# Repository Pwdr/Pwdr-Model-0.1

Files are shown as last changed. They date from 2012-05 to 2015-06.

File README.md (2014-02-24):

#Pwdr Model 0.1

Pwdr is an open source powder-based rapid prototyping machine. Its goal is to promote experiments and innovations in powder-based rapid-prototyping. The machine is ready to use both the 3DP as the SLS process with minimal adaption, although the printer is currently prepped for 3DP.

##Hardware

The Pwdr Model 0.1 consists of chassis, tool head and electronics. The printer entirely consists of off-the-shelf components. It has a simple design and can be built within a couple of hours. The machine is easy and affordable to build and modify. Building a Pwdr Model 0.1 machine costs about €1000,-.

##Software

The accompanying software for the Pwdr Model 0.1 converts the CAD model in a printable format. This file is then uploaded to the Pwdr Model 0.1 micro-controller. The machine is controlled by easy-to-use software that allow full control of the printing process.The Pwdr Model 0.1 software has been based on open source tools like [Arduino](http://arduino.cc) and [Processing](http://processing.org).

##Materials

A whole new range of materials become available for experimenting with open-source rapid-prototyping; for example, when using the 3DP process: gypsum, ceramics, concrete, sugar, etc. And when the SLS process is fully supported, plastic materials like ABS, PP, Nylon and metals become available as building material.A Hewlett Packard inkjet cartridge is used for the deposition of binder. The cartridge can be refilled with custom binders using a syringe. A custom binder of 20% alcohol and 80% water has been proven to work.

##Specifications

- Maximum build size: 125mm x 125mm x 125mm
- Print resolution (3DP): 96DPI
- Minimum vertical step size: 50μm
- Speed (depending on printed part): ±1 minute per layer

### License
This work is licensed under the Creative Commons Attribution-NonCommercial 3.0 Unported License. To view a copy of this license, visit http://creativecommons.org/licenses/by-nc/3.0/.

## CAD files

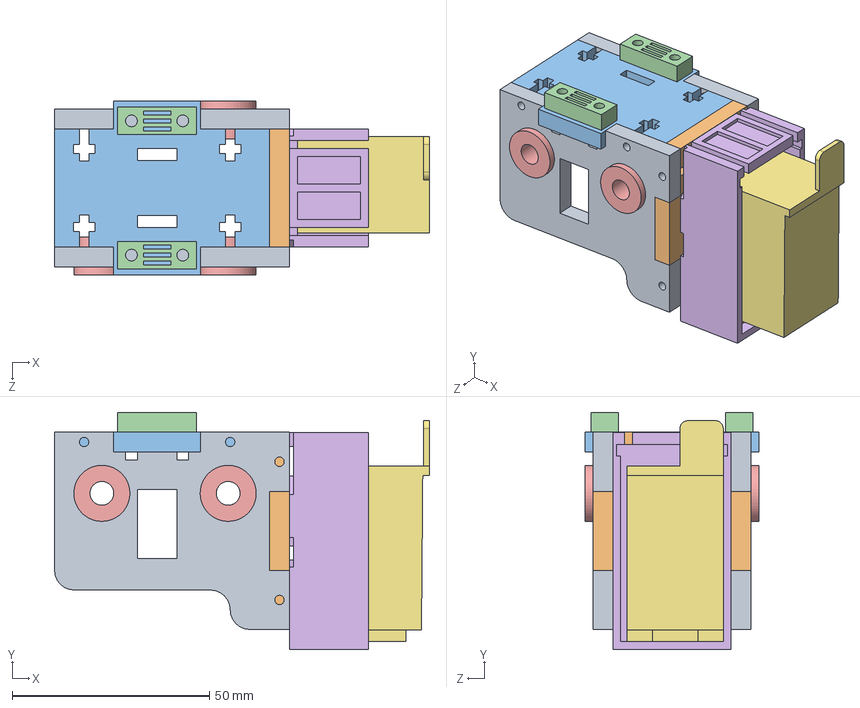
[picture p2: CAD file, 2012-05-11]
CAD drawings/Solidworks/Pwdr - Model 0.1 - XYcarriageMiddle.SLDASM
95.0 x 60.1 x 44.0 mm
Pwdr - Model 0.1 - XYcarriage4 x 2
Pwdr - Model 0.1 - XYcarriage5
Pwdr - Model 0.1 - XYcarriage6
Pwdr - Model 0.1 - XYcarriage7 x 2
Pwdr - Model 0.1 - BronzeBushing6mm x 3
HPC6402CartridgeHolder
HPC6402Cartridge
Pwdr - Model 0.1 - BrassInsert x 4

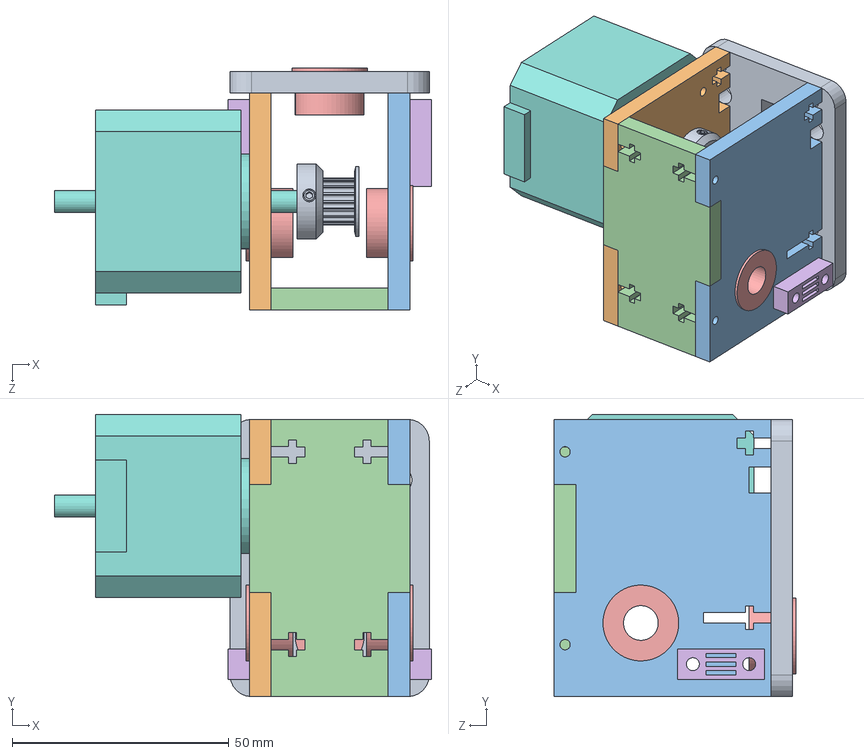
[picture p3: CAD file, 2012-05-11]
CAD drawings/Solidworks/Pwdr - Model 0.1 - XYcarriageLeft.SLDASM
87.0 x 65.2 x 55.8 mm
Pwdr - Model 0.1 - XYcarriage1
Pwdr - Model 0.1 - XYcarriage2Var
Pwdr - Model 0.1 - XYcarriage2Var2
Pwdr - Model 0.1 - XYcarriage3VAR
Pwdr - Model 0.1 - BronzeBushing10nn x 3
Pwdr - Model 0.1 - XYcarriage7 x 2
Pwdr - Model 0.1 - BrassInsert x 4
Nanotec - ST4209S1006-B
A6A51M018DF0606

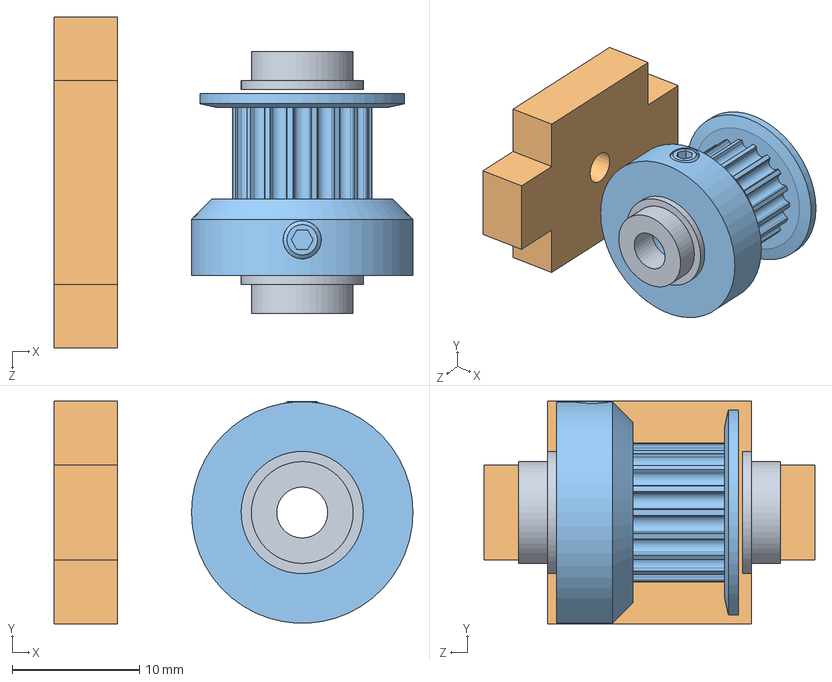
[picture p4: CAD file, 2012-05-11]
CAD drawings/Solidworks/Pwdr - Model 0.1 - BeltTensioner.SLDASM
28.2 x 17.5 x 26.0 mm
Pwdr - Model 0.1 - XYcarriageBeltPropulsion3
Pwdr - Model 0.1 - BronzeBushing5 x 2
A6A51M018DF0606

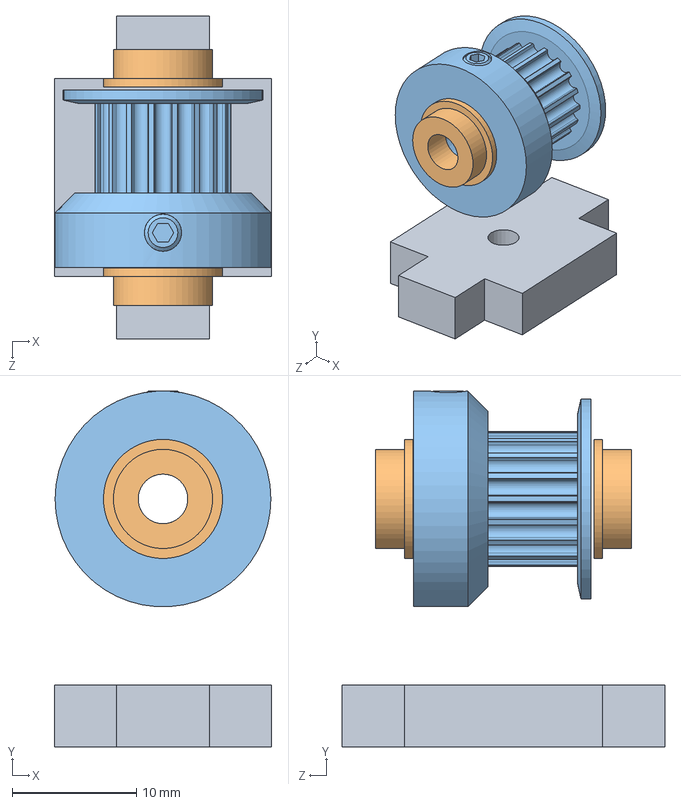
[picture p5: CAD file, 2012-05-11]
CAD drawings/Solidworks/Pwdr - Model 0.1 - BeltTensioner2.SLDASM
17.5 x 28.7 x 26.0 mm
A6A51M018DF0606
Pwdr - Model 0.1 - BronzeBushing5 x 2
Pwdr - Model 0.1 - XYcarriageBeltPropulsion3

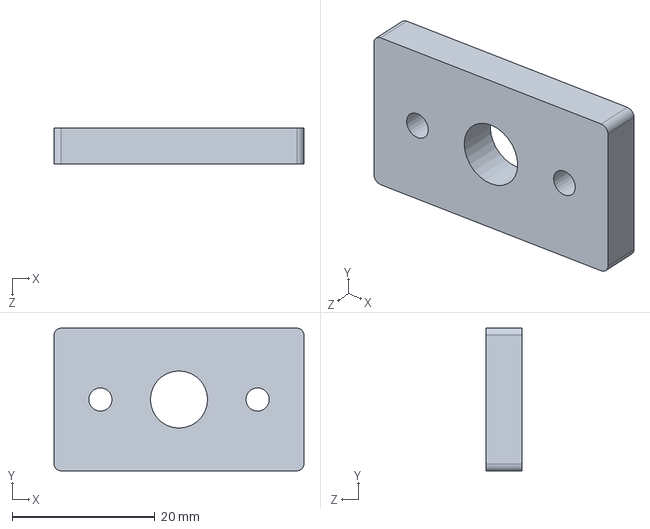
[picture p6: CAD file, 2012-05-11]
CAD drawings/Solidworks/Pwdr - Model 0.1 - CarriageRodHolder.SLDASM
35.0 x 20.0 x 5.00 mm

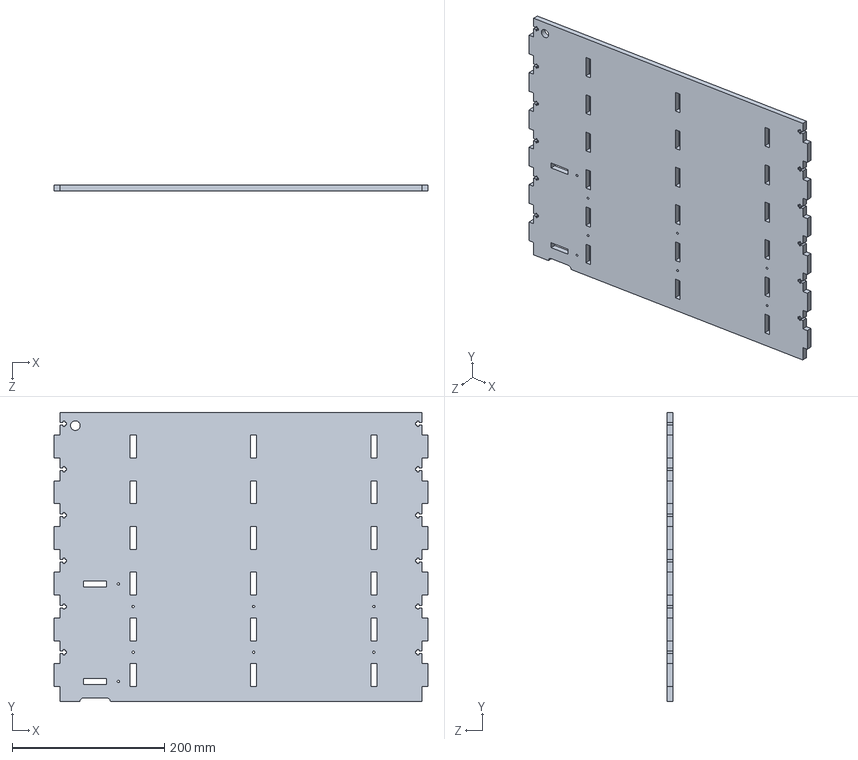
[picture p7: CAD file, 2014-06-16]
CAD drawings/Solidworks/Pwdr - Model 0.1 - Chassis2VAR.SLDPRT
491.0 x 380.0 x 8.00 mm

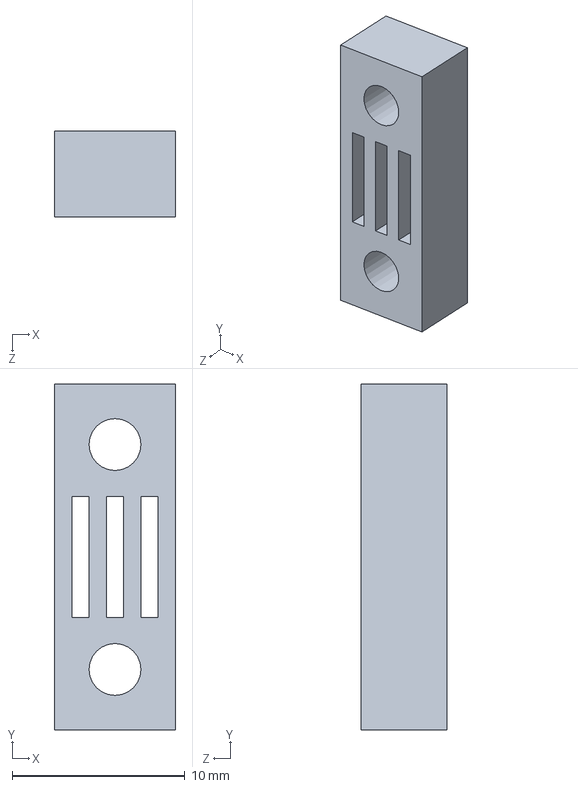
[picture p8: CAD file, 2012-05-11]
CAD drawings/Solidworks/Pwdr - Model 0.1 - XYcarriage7.SLDPRT
7.00 x 20.0 x 5.00 mm

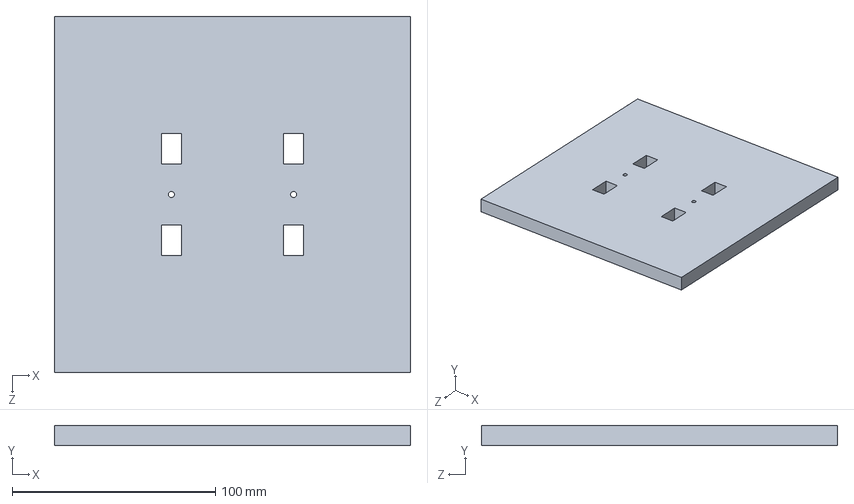
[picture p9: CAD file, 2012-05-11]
CAD drawings/Solidworks/Pwdr - Model 0.1 - BuildPiston1.SLDPRT
175.0 x 10.0 x 175.0 mm

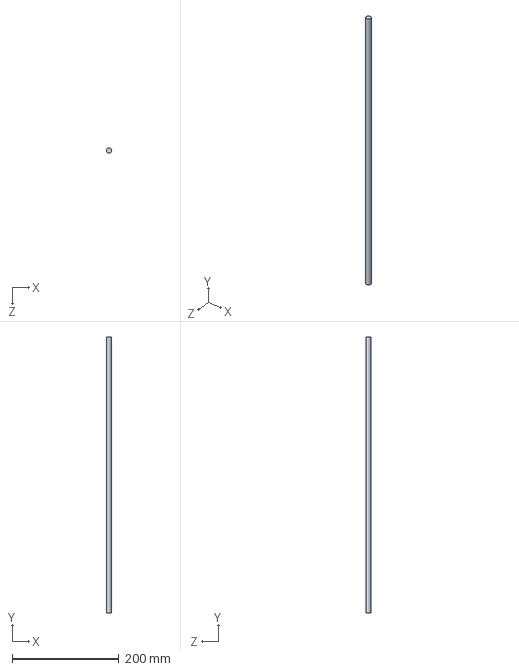
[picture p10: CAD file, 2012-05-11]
CAD drawings/Solidworks/Pwdr - Model 0.1 - XYcarriageRod10mm.SLDPRT
10.0 x 516.0 x 10.0 mm

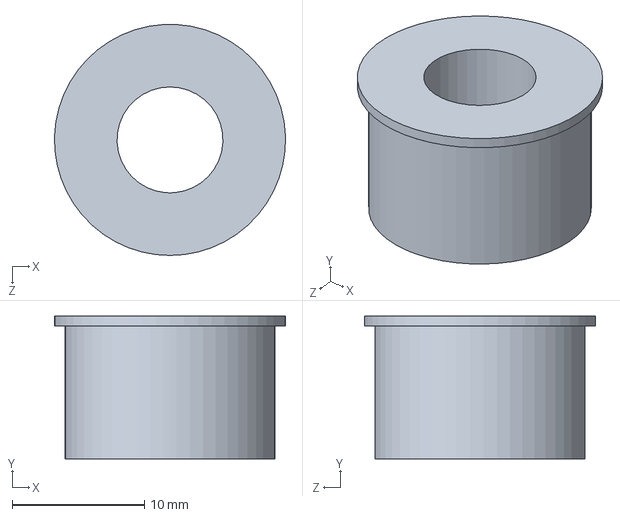
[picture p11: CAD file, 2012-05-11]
CAD drawings/Solidworks/Pwdr - Model 0.1 - BronzeBushing10nn.SLDPRT
17.5 x 10.8 x 17.5 mm

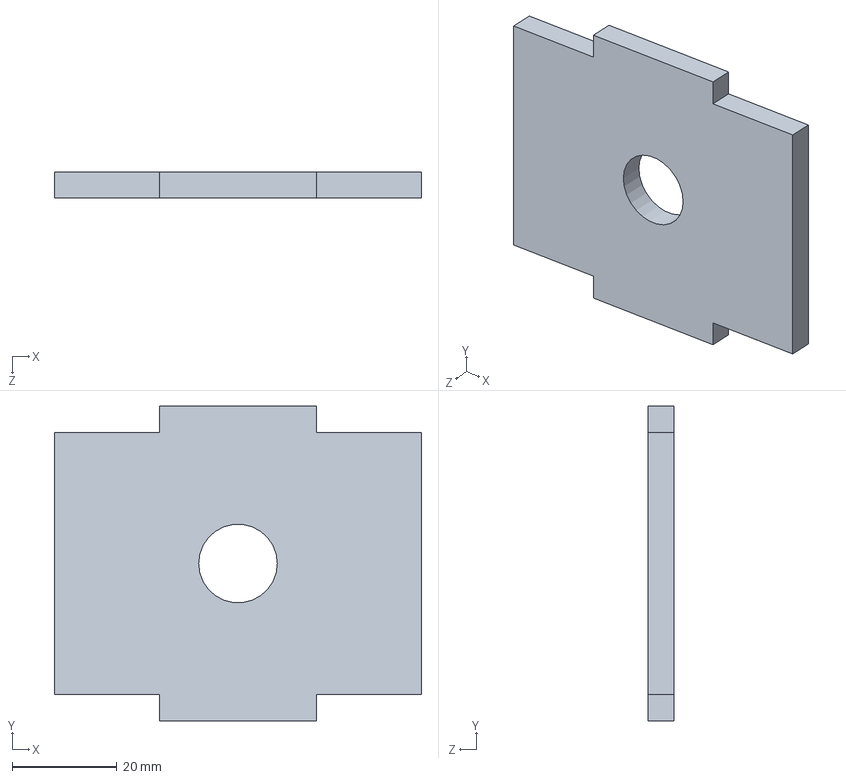
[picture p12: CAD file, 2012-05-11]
CAD drawings/Solidworks/Pwdr - Model 0.1 - BuildPiston3.SLDPRT
70.0 x 60.0 x 5.00 mm

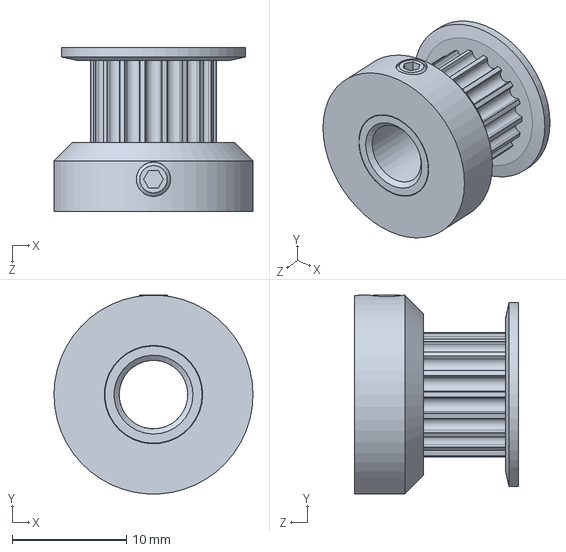
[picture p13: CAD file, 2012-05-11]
CAD drawings/Solidworks/A6A51M018DF0606.SLDPRT
17.4 x 17.4 x 14.3 mm

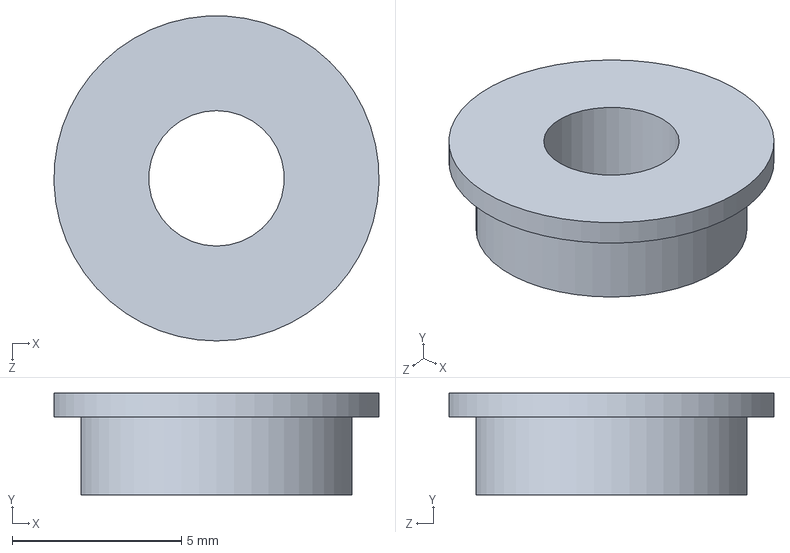
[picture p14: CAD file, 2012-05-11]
CAD drawings/Solidworks/Pwdr - Model 0.1 - BronzeBushing5.SLDPRT
9.60 x 3.00 x 9.59 mm

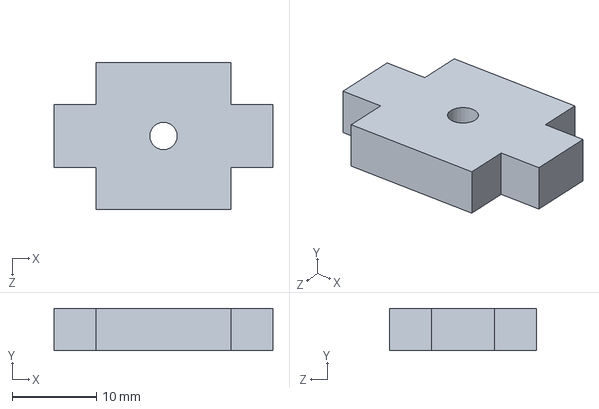
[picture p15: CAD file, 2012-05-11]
CAD drawings/Solidworks/Pwdr - Model 0.1 - XYcarriageBeltPropulsion3.SLDPRT
26.0 x 5.00 x 17.5 mm

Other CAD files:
CAD drawings/Solidworks/Pwdr - Model 0.1 - BuildPiston.SLDASM
CAD drawings/Solidworks/Pwdr - Model 0.1 - Chassis4VAR.SLDPRT
CAD drawings/Solidworks/Pwdr - Model 0.1 - XYCarrigeBelt.SLDPRT
CAD drawings/Solidworks/Pwdr - Model 0.1 - XYcarriage4.SLDPRT
CAD drawings/Solidworks/A7Z44MPSD04MAF.SLDPRT
CAD drawings/Solidworks/Arduino Mega 2560.SLDPRT
CAD drawings/Solidworks/HPC6402Cartridge.SLDPRT
CAD drawings/Solidworks/HPC6402CartridgeHolder.SLDPRT
CAD drawings/Solidworks/Nanotec - LS4118S1404-T5x5-150.SLDPRT
CAD drawings/Solidworks/Nanotec - LSNUT-T6X2-F.SLDPRT
CAD drawings/Solidworks/Nanotec - ST4209S1006-B.SLDPRT
CAD drawings/Solidworks/Pwdr - Model 0.1 - Bearing10nn.SLDPRT
CAD drawings/Solidworks/Pwdr - Model 0.1 - BrassInsert.SLDPRT
CAD drawings/Solidworks/Pwdr - Model 0.1 - BronzeBushing6mm.SLDPRT
CAD drawings/Solidworks/Pwdr - Model 0.1 - BuildPiston2.SLDPRT
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

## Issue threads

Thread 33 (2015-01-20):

Y axis distance

MasseyAlbany, 2015-01-20:
Hi,

I am having issues while testing with the distances traveled, specifically by the Y axis. When I press print, it starts printing at the zero position (where it is when power is connected). It prints the first layer fine, but then when it goes to spread a new layer it goes all the way to the end and then jams against the edge. This means that either it is set to move too far or I am doing something wrong in my set up before I press print.

Please help me

Pwdr, 2015-01-20:
Just to check: do you perform the correct homing procedure? Step 1: move
carriage to far end (by hand, no power) Step 2: enable power, click 'Home'
in the GUI.

If you've done that, and the carriage still jams the other end, then adjust
the following parameters:

const long build_piston_length = 28000/stepY;
const long distance_roller_nozzle = 30000;
const long build_piston_end_stop = 76000;

On Tue, Jan 20, 2015 at 1:08 AM, MasseyAlbany <notifications@github.com>
wrote:

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

MasseyAlbany, 2015-01-20:
Do you mean the "initial position" button? If I press that after connecting the power the head moves along the Y axis about 85% of the way (to the left). Then when I press "print file" it starts printing and moving the Y axis, still moving to the left. This means it jams while trying to print the file because it only has a small amount of movement before it hits the end. However if I do not press the "initial position" button, it starts printing where it is, and moves to the left. Even if I start it at the right end, so that it has the entire length to move, it still jams when doing a new layer.

I will have a play with the code you mention above and see what happens with the distances traveled.

Closed 2015-06-10.

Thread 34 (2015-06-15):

Printing materials/binders

MasseyAlbany, 2015-06-15:
Hi,

I have my PWDR printer running now but am struggling to get any parts out of it which seems to be an issue with the powder/binder combination. I am using a Nylon powder used in our SLS machine and it seems to be too fine to properly bind with the standard ink.

I was just wondering what materials and binders other people have had success with and where they were sourced. I'm specifically looking into ceramics now but want to try other media too.

Thanks.

MatthiasWM, 2015-06-15:
SLS is a different system using heat to sinter the powder. PWDR uses a chemical binding process with a special powder/binder combination. See here:

https://en.wikipedia.org/wiki/Powder_bed_and_inkjet_head_3D_printing

http://depts.washington.edu/open3dp/category/formulas/

http://reprap.org/wiki/Powder_Printer_Recipes

and here

http://ytec3d.com/plan-b-printing-materials/

Pwdr, 2015-06-26:
You won't be able to print Nylon with the standard ink from the HP C6602
cartridges. But you can fill the cartridges up with aceton or similar (and
aggressive) fluids. The C6602 is known to withstand it.

Please take a look at our paper on the Pwdr machine, which includes a
section on producing ceramics parts:
http://www.sciencedirect.com/science/article/pii/S2212827113001753

Alex

On Mon, Jun 15, 2015 at 9:18 AM, MatthiasWM <notifications@github.com>
wrote:

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

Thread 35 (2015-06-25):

Arduino Setup and Belts

KH-Xavier, 2015-06-25:
Hello!

I am from the University of Alberta and we are excited to be building not only one, but several of these machines for research if the first one works. However, I am having some difficulty...

1. After much fiddling, Processor now will talk the Arduino (I believe), however, whenever I try to "Convert Model" I receive the error "ArrayIndexOutOfBoundsException:521216"

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

Also, after selecting the right COM, I receive "SD Initialization Failed." Does the SD card need to be hard-wired in before the program will work? I am trying to program the Arduino while I wait for parts to come in the mail...

2. Any suggestions on where to get the small belts for the gears? I can't find much smaller than 60 mm and some require 40-50 mm on the carriages.

Thanks!

Pwdr, 2015-06-26:
Hi there,

Great to hear there is a lot of interest in the Pwdr project for
educational purposes! I'm pretty confident that together, we'll be able to
fix your problems.

1. Normally, it shouldn't bee too much of a hustle to get the serial
communication. Maybe you can give me some details what you had to fiddle
with? But back to your question. This error pops up more often, I'm still
not sure what is the root cause, but it has to too with the STL file. Some
files just don't work. This teapot (https://www.thingiverse.com/thing:852078)
should work.

2. Yep, the SD card should be connected to the Arduino, at least to print
something. You can still jog the axes when the SD Initialisation Failed
pops up (well, I think so, have to check the source code)

3. I got my belts and pulleys from SPD-SI (http://www.sdp-si.com), as shown
in the BOM, but there should be plenty of similar options around, for
example McCaster-Carr (http://www.mcmaster.com/). You mention some measures
(40-50mm and 60mm), but I'm not really sure what you mean, can you explain?

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

KH-Xavier, 2015-06-26:
Thanks for the quick response.

1. I changed the serial communication to the correct COM port (next time I am in the lab I can provide which lines I changed), but the Processing window allowed me to select Serial #2 (COM6) with ease. However, I then received an "RXTX version mismatch" error, so a quick Google led me to

http://forum.processing.org/one/topic/how-do-i-install-rxtx-2-2pre1-jar-on-windows-7.html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

I followed the instructions and the error disappeared.

I will try to convert the teapot file when I'm in the lab and let  you know if it works.

2. Great. Once the hardware arrives I will try to jog the axes without printing. I see an Eagle schematic, but is there an Eagle .brd file that is successful? I am trying to make my own PCB board for elegance, but I'm worried something will cross incorrectly and cause hours of frustration...

3. I ordered the belts from SDP-SI as per the BOM in the documentation, but I see that there is a huge belt that looks too large for the printer (2218mm)? In terms of the small belts, here's a screen shot of what I mean by the small belts.

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

I looked again and found small belts that will work.. guess I didn't look hard enough. I will order the correct sizes as I build the printer.

Pwdr, 2015-06-27:
COM port behavior on windows is a bit quirky. I'll add some information
about the RXTX upgrade.

There is no .brd available. Currently there is a error in the schematics,
I'll update is asap. Could you share the design of the PCB when it's
finished?

The huge belt isn't used as such, it has to be cut to length and tensioned
using the clamping parts. The smallest belt should fit. The chassis has
slotted holes to make it fit.

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

Pwdr, 2015-06-27:
The diagram has been updated!

On Sat, Jun 27, 2015 at 12:53 PM, Alex Budding <alex.budding@gmail.com>
wrote:

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

KH-Xavier, 2015-06-27:
Thanks for that.

It looks like the only change is the HP connector? Can you confirm that Output 5 of U6 is disconnected?

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

Pwdr, 2015-06-27:
No, that's not correct, thanks for checking out the complete diagram. This
is how the wiring should be. I've commited the update.

[image: Inline image 1]

The only change (*prior this hickup*) was in this area:

[image: Inline image 2]

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

KH-Xavier, 2015-06-27:
For some reason your images aren't showing. I'll work on a .brd from your new .sch file.

KH-Xavier, 2015-06-29:
I made it to the lab today and as promised, this is what I changed in the code...

Under PWDR_GUI_V0_3.pde > Serial

String[] comList;
int selectPort;
boolean serialSet = false;
Serial arduinoSerial;

String serialString = "Choose the correct Arduino COM port...";

void startSerial(){
  arduinoSerial = new Serial(this, "COM6", 9600);
  arduinoSerial.bufferUntil(10);
  serialSet = true;
  serialString = "Serial port #"+selectPort+" connected";

The only thing I changed was to hard code "COM6", rather than selecting it.

I tried converting the Utah Teapot and it worked flawlessly.... I didn't bother trying to send the data because there is no electronics yet.

I will be uploading the .brd shortly.

KH-Xavier, 2015-06-29:
Also, Boreaz published a different schematic for the HP Connector in Issue #22. What's the difference between that and the one you published a few days ago?

Which end of the connector is labelled 16? On my cable, two pins on the end are connected as below, which pin does this correspond to? Are they labelled 1 to 16 or 16 to 1?

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

KH-Xavier, 2015-07-14:
Hi there,

I've been working on Pwdr again and the PCB has been hooked up, along with the motor drivers.

When I use the Processor program, it won't let me select the correct COM. I see the available COM ports, but when I click the box nothing happens. Even after I changed the code above, it still says Arduino not connected. This is with or without the PCB...

KH-Xavier, 2015-08-06:
Could I please get an update?

Pwdr, 2015-08-06:
Sorry, I returned from vacation this week, your message was quite down the
large pile of to-do's.

Here is an image of the numbering on the ribbon, print head and catridge
holder:

I'm quite puzzled now about the schematics. Currently, I don't have
physical access to my Pwdr machine in order to check it. Maybe Boraz can
confirm his design works? Or maybe it might even be safer to check on the
old layout (
https://github.com/Pwdr/Pwdr-Model-0.1/blob/6084e1437b6733d2ed041ac12901771d7d181411/Electronics/Pwdr-Circuit-0.1.pdf
)

Concerning the COM issue: can you connect to the Arduino using a simple
Processing sketch? On what platform are you? Have you installed the RTRX
update?

Alex

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

KH-Xavier, 2015-08-06:
No worries.. you're just my only savior at this point!

For some reason the image won't show.. can you hotlink it?

The COM issue has been sorted out. I can connect now... but now the Utah Teapot is giving me the Array Index Out of Bounds error... I'm going to try and get some coding colleagues to look at it if possible. I haven't touched the code and it was working before.

Pwdr, 2015-08-06:
I fixed the image in my previous post.

I'm not 100% sure the teapot I linked does work, here is a link to the teapot I always use: http://wetterhorn.nl/teapot.stl

Pwdr, 2015-08-06:
My schematics was based on this:

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

Coming from DYI Inkjet Printer (http://www.thingiverse.com/thing:8542)

But that doesn't match with the numbering of the ribbon cable. Vaguely, I remember the connector Conn_16_hp_q2347A to be the socket for the ribbon. So the numbering in the schematic should be like in the picture of the ribbon (NC/NC/COM/3/4/5/2/1/12/11/10/9/6/7/8)
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
Pwdr, 2015-08-17:
What's the distance between the nozzles and the paper? When it's more than
(roughly) one centimeter, it sprays.

But! The cartridge definitely shouldn't smoke, were is the smoke coming
from?

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

KH-Xavier, 2015-08-17:
I moved the paper closer by hand and it was a stream... that was an easy fix, thanks.

As for the smoke, it's coming from the nozzles. Here's a picture, you can see the smoke, slightly, against the black plastic near the nozzles. It's only when ink is being jetted. No clue. I'm tempted to just leave it, but I don't want a colleague to be subjected to an ink grenade.

Again, I raised the voltage slightly to see what would happen and ink jets at ~20V instantly, but smoke still happens. Maybe the current is too high? Not sure what throwing resistors down would do.

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

Pwdr, 2015-08-17:
Looks pretty cool, but indeed, you might not want to risk redecorating your
office.

Couple of things to try: to lower the voltage or even adjusting the timing
in the Arduino program. Measure the resistance and compare with a pristine
cartridge.

PS: Have a look at this: microwavecam.com/Videos/Misc/color ink cartridge
211b.wmv :-)

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

Boreaz, 2015-08-17:
@KH-Xavier  Wow this is scary, try to increase this https://github.com/Pwdr/Pwdr-Model-0.1/blob/master/Arduino/PwdrFirmware2_0/voidsController.ino#L69

KH-Xavier, 2015-08-19:
@Pwdr - your video would definitely be what our lab would have looked like if I let this cartridge run...

@Boreaz - I increased the value, but anything higher than 1000 and the ink just turns into big droplets and makes a mess; the smoke is also still there... I think it might be a damaged cartridge from all the smoke earlier. I ordered new ones, let us see what happens then.

soulkiller2001, 2015-12-24:
Hello!I just met some problem.When  I try to convert my model,it just show error as~~~Can you tell me how to solve this problem?
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

Pwdr, 2015-12-25:
It has got something to do with different STLs. Unfortunately, I haven't
been able to fix it... :-(

Please try another STL and see whether it works

On Thursday, 24 December 2015, soulkiller2001 <notifications@github.com>
wrote:

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

kelyaman, 2017-06-28:
hi guys,

can anyone explain this lines,  i have got a Problem to adjust my Steppers

// Size of steps for stepper motors  ( steps pro revolution
const int stepX = 21;    //21;       // 0.09433962264 mm  per step (5*9.6mm*PI/1600)
const int stepY = 250;   //500;      // 0.09433962264 mm  per step (5*9.6mm*PI/1600)
const int stepZ = 120;   //120;      // 0.1mm per full stap (10*0.01)

// Size of steps when jogging
const int jogStepY = 1000;
const int jogStepX = 500;
const int jogStepZ = 250;

// Size of machine in steps. Type long because number of steps > int (2^15)
const long build_piston_width = 11000/stepX; //11000/stepX;       //2000/stepX  total width: 14800
const long build_piston_length =28000/stepY; // 28000/stepY;      // total length 76000
const long distance_roller_nozzle = 30000; //30000;
const long piston_depth = pwdrconfig[3];        // The depth of the part is defined by the preprocessor
const long build_piston_end_stop = 76000; //76000;          // Absolute end of the machine

Pwdr, 2017-06-28:
These lines define how many steps the stepper motor need to turn (in X and
Y) during printing, in order to print with a resolution of 96DPI

The steps in Z direction control the layer thickness of the powder

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

kelyaman, 2017-06-28:
Kannst du mir bitte noch eine Skizze mit die Formeln die ich benötigen kann?

Ich studiere fahrzeugtechnik, daher bin ich mit dem Thema 3D Drucker
übergefragt.

Danke mehrmals

Am 28.06.2017 11:59 vorm. schrieb "Pwdr" <notifications@github.com>:

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

kelyaman, 2017-07-05:
pleez I have a question, do I need a Library to control my Ink,

whats mean those lines:

void spray_ink( byte lower_nozzles, byte upper_nozzles) {
//lower_nozzles = 1-8  - PORTA
  for(int i = 0; i <= 7; i++){
    byte mask = 1<<i;
    if(lower_nozzles & mask){
      PORTA |= mask; delayMicroseconds(5);
      PORTA &= ~mask; delayMicroseconds(1);
    }
  }
//upper_nozzles = 9-12 - PORTC using pins 4,5,6,7 so 4-7 not 0-3
  for(int i = 4; i <= 7; i++){
    byte mask = 1<<i;
    if(upper_nozzles<<3 & mask){
      PORTC |= mask; delayMicroseconds(5);
      PORTC &= ~mask; delayMicroseconds(1);
    }
  }

bazrabazara, 2017-09-11:
i have problem with convert stl file. I also tried teapot.stl file. and  which CAD program did you draw?.are there any solutions?.

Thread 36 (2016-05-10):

Laser cut Acrylic

ChinaShopBull, 2016-05-10:
Do you have any advice for someone in the United States for modifying the design to accommodate the sizes of acrylic sheet that are available here? It turns out that 4.5 mm and 9 mm are the most common sizes close to your spec. I don't really relish the idea of redesigning the chassis, and I'm wondering if I can get away with sanding down some of the tabs to fit, or adding shims where necessary.

MatthiasWM, 2016-05-10:
> On May 10, 2016, at 2:17 AM, ChinaShopBull <notifications@github.com> wrote:
>
> Do you have any advice for someone in the United States for modifying the design to accommodate the sizes of acrylic sheet that are available here? It turns out that 4.5 mm and 9 mm are the most common sizes close to your spec. I don't really relish the idea of redesigning the chassis, and I'm wondering if I can get away with sanding down some of the tabs to fit, or adding shims where necessary.

I did redesign most of the part, but unfortunately not for U.S. sizes, but for different metric sizes.

I agree that this is annoying, but it is relatively easy to do if yu have somewhat of a feel for CAD. Sure, you can also sand and shim, but modifying the CAD data seems much less work. Acrylic is almost impossible to sand, and shims will make everything weak.

You are probably fine if all you do is change the size of the slots. No real need to lengthen or shorten the tabs.

There are few truly citical parts. Make sure that the pistons still fit inside the cylinders.

Pwdr, 2016-05-11:
Fully agree with MatthiasWM.

If you don't have access to CAD, you could even change the SVG/DXF with a
vector editor, as only the slots need to be changed.

On Tue, May 10, 2016 at 10:55 PM, MatthiasWM <notifications@github.com>
wrote:

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

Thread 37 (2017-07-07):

This Project ist a fake

kelyaman, 2017-07-07:
pleeeze do not waisting your time to buid this 3D Printer,
everything is false.

s'il te plais ne perds pas ton temps pour construire c'ette imprimant 3D
tous les dossiers sont faux.

bitte, verschwinden Sie Ihre zeit nicht um diese 3D brucker nachzubauen,
alle files sind falsch.

رجاءًَ لا تضيعو وقتكم في تركيب هذه الطابعة 3د.
فكل المعطيات خاطئة

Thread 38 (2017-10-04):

Usage of firmware, please help me out

Casssss, 2017-10-04:
Hello,

I have been trying to find the right software to operate a pwdr inkjet printer and translate a .stl file to readable instructions. The printer consists of 5 stepper motors (X, Y, Z, Z2, Roller). I am using an Arduino MEGA 2560. I am completely new to this and am still trying to become familiar with the language.

So the firmware2_0 file does not include the rest of the arduino files. Which of these do I need for operating the motors and how do I combine them into uploadable firmware?

Also does anyone have a reccomendation on which slicer to use?

Any help is greatly appreciated.

Pwdr, 2017-10-04:
Hi Casssss,

Most questions will propably be answered as soon as you read through the
user manual: http://pwdr.github.io/usermanual.html

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

Casssss, 2017-10-11:
Thanks for the quick response. I figured most of it out now.

Closed 2017-10-10.

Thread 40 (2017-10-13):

Error when connecting to COM port

Casssss, 2017-10-13:
Hi all,
I am trying to use the GUI_V0_3, I have an arduino MEGA2560 attached that is not yet connected to the printer and I use processing 1.5.1. When I click the connection tab in the interface after converting this warning pops up in the message window:
WARNING:  RXTX Version mismatch
	Jar version = RXTX-2.2pre1
	native lib Version = RXTX-2.1-7

I have followed the steps described in this link and added rxtx-2.1-7-bins-r2.zip to the processing :
https://forum.processing.org/one/topic/how-do-i-install-rxtx-2-2pre1-jar-on-windows-7.html#25080000000981023 but it doesn't seem to change anything.

When I ignore the warning and click the COM port that connects my arduino, the following error comes up:
Exception in thread "Animation Thread" java.lang.ArrayIndexOutOfBoundsException: 1
	at Pwdr_GUI_V0_3.startSerial(Pwdr_GUI_V0_3.java:498)
	at Pwdr_GUI_V0_3.mouseClicked(Pwdr_GUI_V0_3.java:1056)
	at processing.core.PApplet.handleMouseEvent(Unknown Source)
	at processing.core.PApplet.dequeueMouseEvents(Unknown Source)
	at processing.core.PApplet.handleDraw(Unknown Source)
	at processing.core.PApplet.run(Unknown Source)
	at java.lang.Thread.run(Thread.java:662)
I have already filled in the correct serial port (COM3) at line 6 of the serial tab.
Is this familiar to anyone?

Closed 2017-10-18.

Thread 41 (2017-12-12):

Calibration issues

Casssss, 2017-12-12:
Hi all,

I am using an arduino 2560, a RAMPS 1.4 and an inkshield (http://nicholasclewis.com/projects/inkshield/theory/) to operate the pwdr printer.

I have been trying to understand the firmware and processing GUI in order to calibrate the printer but despite best effort, I am still quite newby when it comes to software.
The usersmanual states ''Currently, the only way to change the parameters is by hardcoding them in the Arduino parameter declarations''
To me that sounds like the stepsize should be changed in the firmware, however I can only make the steppers move using the Processing GUI individualy which doesn't necessarily have anything to do with the declerations in the firmware. Can someone point me in a direction?

Help is appreciated,
Cas van Schaik,

Pwdr, 2017-12-12:
The stepSize van be changed in the Arduino firmware source, after that, it
needs to be uploaded to the Arduino Mega.

The stepSize determines how much the printhead moves, basically controlling
the printer resolution.

If you were able to move the steppers in the GUI, the connection/interface
between Arduino and RAMPS is fine.

You mention you’d like to calibrate your printer, could you point out what
exactly you’d like to do?

Thanks,
Alex

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

Casssss, 2017-12-14:
Hi Alex,

I thought the stepsizes had to be changed to make the stepper motors move similar distances relative to each other which is what I meant with calibration.

Initially I thought the jogsteps of the GUI were defined in the firmware but that doesn’t seem to be the case since the GUI and firmware work fine individually, I can’t seem to connect the GUI with the serial port after uploading the firmware, an error pops up when I click the serial port but only if the firmware is running already.

There is one other thing that makes me scratch my head, I got the inkshield from N.L. and the RAMPS board, I am trying to stack them both onto the MEGA. When I look at the picture underneath it looks like the inkshield is stacked on the Arduino but the RAMPS isn’t. May I ask how you managed to connect both boards to the MEGA?

[P4118757]
Thanks for your quick reply, it helps a lot.

Kind regards,
Cas van Schaik

Van: Pwdr<mailto:notifications@github.com>
Verzonden: woensdag 13 december 2017 06:39
Onderwerp: Re: [Pwdr/Pwdr-Model-0.1] Calibration issues (#41)

The stepSize van be changed in the Arduino firmware source, after that, it
needs to be uploaded to the Arduino Mega.

The stepSize determines how much the printhead moves, basically controlling
the printer resolution.

If you were able to move the steppers in the GUI, the connection/interface
between Arduino and RAMPS is fine.

You mention you’d like to calibrate your printer, could you point out what
exactly you’d like to do?

Thanks,
Alex

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

—
You are receiving this because you authored the thread.
Reply to this email directly, view it on GitHub<https://github.com/Pwdr/Pwdr-Model-0.1/issues/41#issuecomment-351127225>, or mute the thread<https://github.com/notifications/unsubscribe-auth/AeqJ5M5z5rS5KXbk_ZBjHGQsQ3bS-e0Jks5s_rpNgaJpZM4Q-TYB>.

Pwdr, 2017-12-18:
Instead of a RAMPS, I've used a custom proto shield...

Please send me a PM, so I can help you in Dutch :-)

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

Casssss, 2017-12-20:
I have send an Email to pwdr yesterday if that's what you meant by PM, I am not sure if it arrived.

Pwdr, 2017-12-20:
Mmm, I cannot find your email. Did you use the address mentioned on
pwdr.github.io?

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

Casssss, 2018-01-09:
Ah shit than you probably haven’t received my last one either, this adress right? pwdr@wetterhorn.nl<mailto:pwdr@wetterhorn.nl> Sorry could you send me an email?

Vriendelijke groeten,
Van: Pwdr<mailto:notifications@github.com>
Verzonden: donderdag 21 december 2017 10:44
Aan: Pwdr/Pwdr-Model-0.1<mailto:Pwdr-Model-0.1@noreply.github.com>
CC: gus<mailto:schaikvancas@outlook.com>; Author<mailto:author@noreply.github.com>
Onderwerp: Re: [Pwdr/Pwdr-Model-0.1] Calibration issues (#41)

Mmm, I cannot find your email. Did you use the address mentioned on
pwdr.github.io?

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

—
You are receiving this because you authored the thread.
Reply to this email directly, view it on GitHub<https://github.com/Pwdr/Pwdr-Model-0.1/issues/41#issuecomment-353190930>, or mute the thread<https://github.com/notifications/unsubscribe-auth/AeqJ5GKoKx9bit4jdCm-PG3kXMweRF98ks5tCX-fgaJpZM4Q-TYB>.

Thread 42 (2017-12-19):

lawercut drawing files?

Marita89, 2017-12-19:
hi,
I would love to download the lasercut drawings, but they do not seem to be available.
Is it possible to share them again?

Thank you!
best,
Marita

Pwdr, 2017-12-19:
Hi Marita, you'll find the files for lasercutting over here:
https://github.com/Pwdr/Pwdr-Model-0.1/tree/master/CAD%20drawings/Lasercut%20drawings

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

Marita89, 2017-12-20:
thank you, I found this link, but all I can see is this:

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

I expected to see a drawing or is this how it is supposed to be?

Pwdr, 2017-12-20:
You have to zoom in quite a bit in order to see the thin lines.

The orange bounding box is required for the laser cut service I used.

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

Marita89, 2017-12-21:
Thank you for your quick reply!:)

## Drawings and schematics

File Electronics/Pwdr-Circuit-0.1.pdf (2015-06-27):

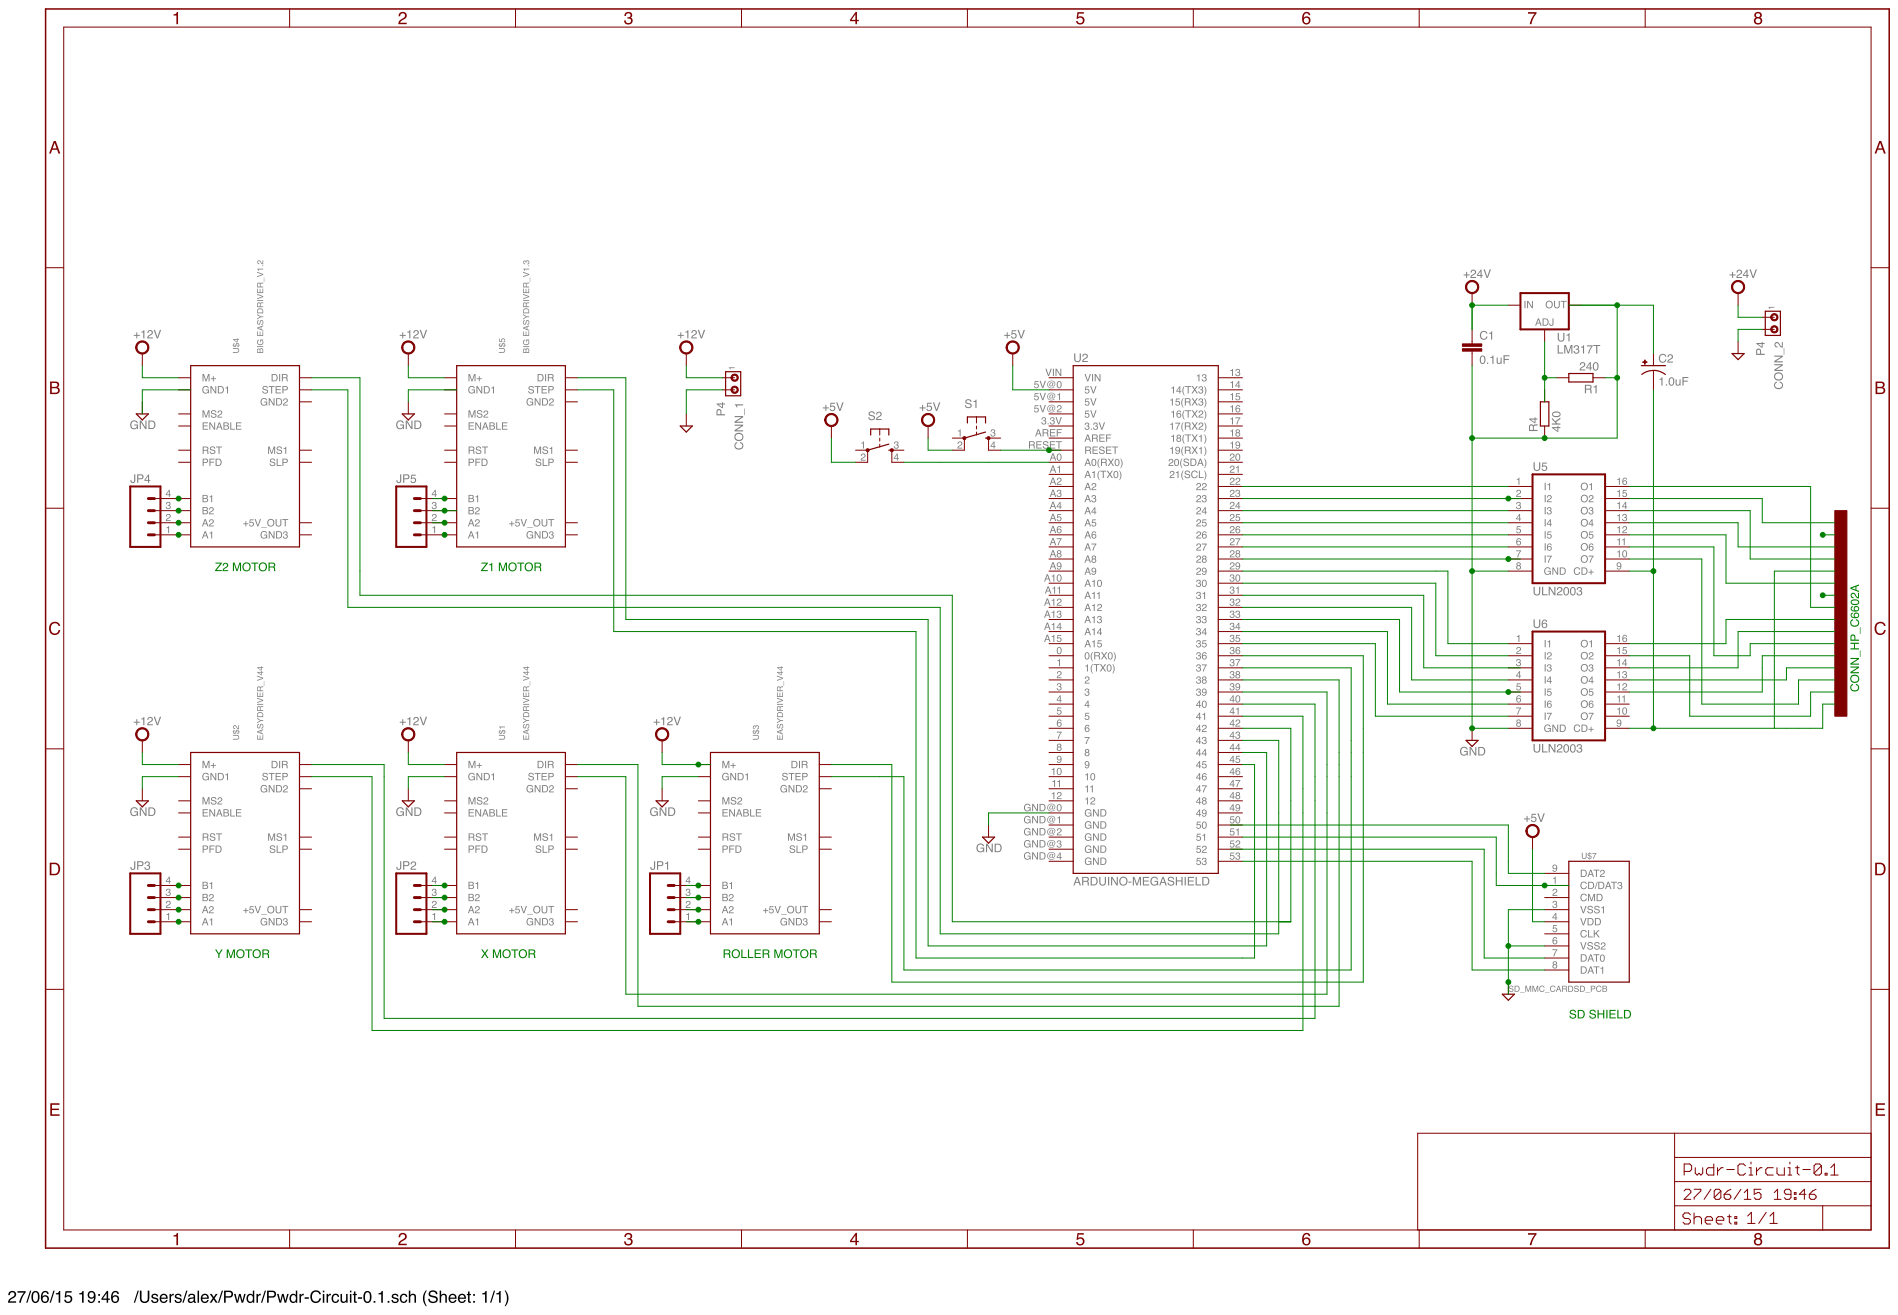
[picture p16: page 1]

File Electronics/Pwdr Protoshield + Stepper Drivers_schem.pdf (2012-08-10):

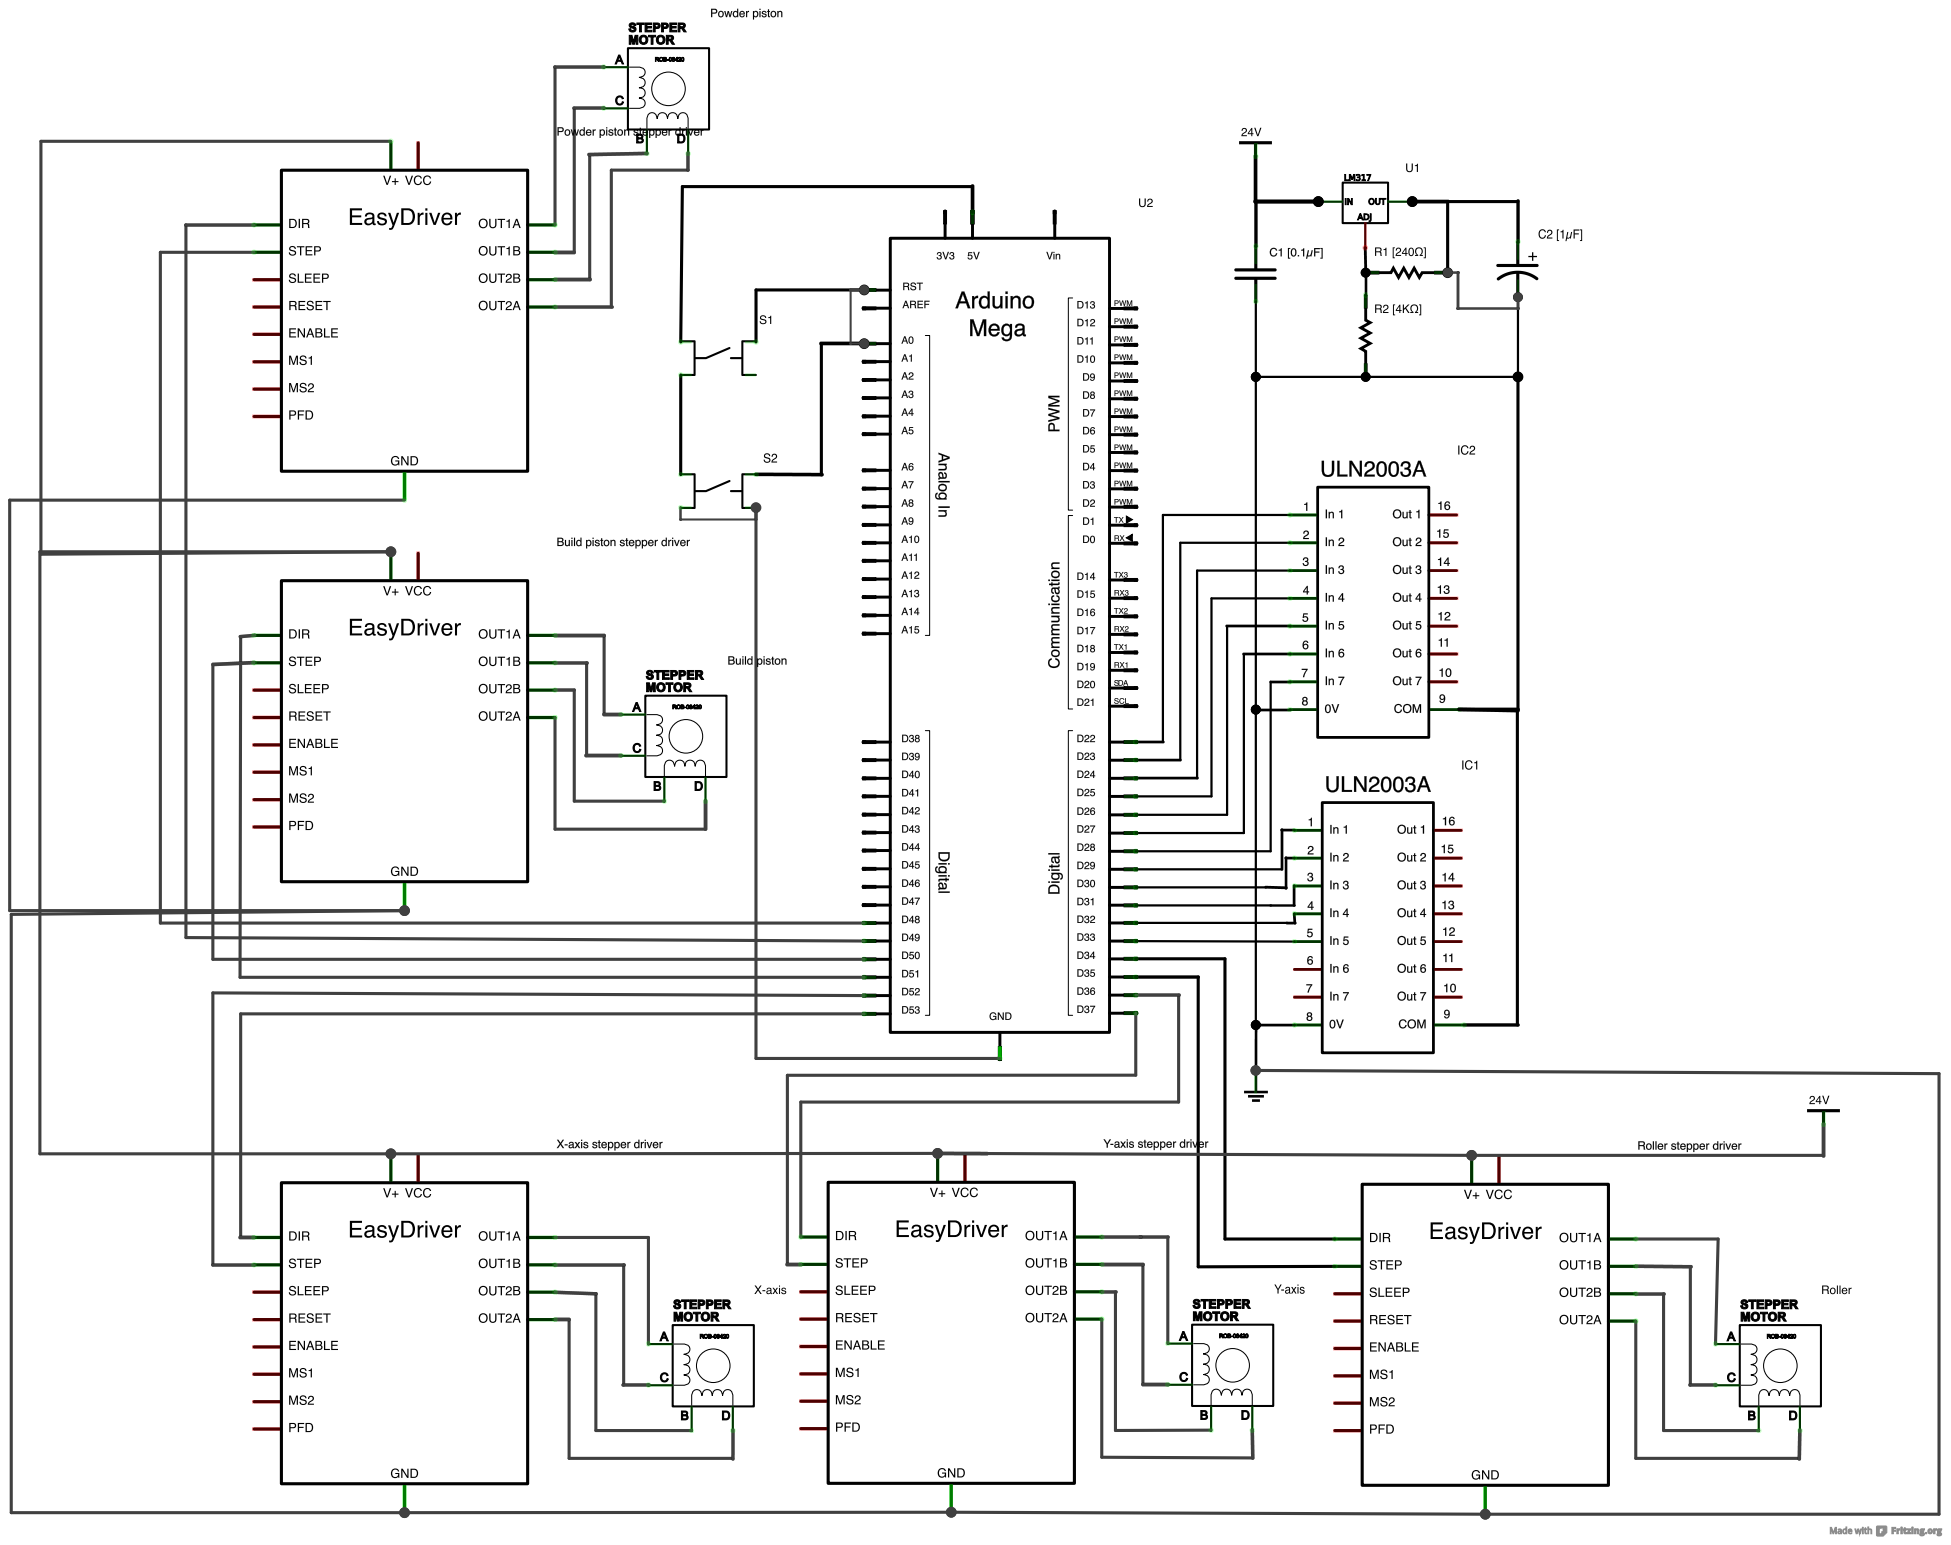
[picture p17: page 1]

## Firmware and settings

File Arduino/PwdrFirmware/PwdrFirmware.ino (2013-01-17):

/*MMMMMMMMMMMMMMMMMMMMMMMMMMMMMMMMMMMMMMMMMMMMMMMMMMMMMMMMMMMMMMMMMMMMMMMMMMMMMM
MMMMMMMMMMMMMMMMMMMMMMMMMMMMMMMMMMMMMMMMMMMMMMMMMMMMMMMMNmmmmmNMMMMMMMMMMMMMMMMM
MMMMMMMMMMMMMMMMMMMMMMMMMMMMMMMMMMMMMMMMMMMMMMMMMMMMMMMM/     /MMMMMMMMMMMMMMMMM
MMMMMMMMMMMMMMMMMMMMMMMMMMMMMMMMMMMMMMMMMMMMMMMMMMMMMMMMhy.   hMMMMMMMMMMMMMMMMM
MMMMMMMMMMMMMMMMMMNNNNMMMMMMMMMMMMMMMMMMMMMMNMMMMMMMNNNNNm   -MMMMMMMMMMNNNMMMMM
MMMMMMMMMy////oNh+:..-oNN/////sMMMN+///MMMMo:/oNMMdo:-.-::   yMy////oMdo:./MMMMM
MMMMMMMMM/-`   /`-:`   od--   /MMN+    MMMs   sMN+` `:++-   .NM/-`   +``..dMMMMM
MMMMMMMMMMM-   :mMMh   :MMM.  /MMo ``  MMy  `yMm-  -dMMMs   oMMMM-   .smmmMMMMMM
MMMMMMMMMMd   -NMMMh   +MMM:  /Ms  s`  Md` `yMM/  `mMMMM-  `mMMMd   .mMMMMMMMMMM
MMMMMMMMMM/   hMMMM+   dMMM/  +h` oN   m. `hMMd   /MMMMh   /MMMM:   dMMMMMMMMMMM
MMMMMMMMMm`  .NMMMy   oMMMMo  /` oMN  .: `hMMMs   sMMMd.   dMMMd   :MMMNddNMMMMM
MMMMMMMMMo   :hdh+` `oNMMMMs    +NMm    .dMMMMs   -hho..  `yyNM/   hMMd.``.hMMMM
MMMMMMMMN`    ``  ./dMMMMMMy   +NMMd   .dMMMMMN:    `:hy.```.MN```-MMMh`  `yMMMM
MMMMMMMMs   +dhyhdmMMMMMMMMNdddNMMMNdddmMMMMMMMNdyyhmNMMNmmmmMNmmmNMMMMmhhmMMMMM
MMMMMNdd.   ydMMddddddddddddddddddddddddddddddddddddddddddddddddddddddddddNMMMMM
MMMMMy``    `.Mm``````````````````````````````````````````````````````````mMMMMM
MMMMMmdddddddmMNddddddddddddddddddddddddddddddddddddddddddddddddddddddddddMMMMMM
MMMMMMMMMMMMMMMMMMMMMMMMMMMMMMMMMMMMMMMMMMMMMMMMMMMMMMMMMMMMMMMMMMMMMMMMMMMMMMMM
MMMMMMMMMMMMMMMMMMMMMMMMMMMMMMMMMMMMMMMMMMMMMMMMMMMMMMMMMMMMMMMMMMMMMMMMMMMMMMMM
MMMMMMMMMMM                                                          MMMMMMMMMMM
MMMMMMMMMMM Firmware for Pwdr three-dimensional powder based printer MMMMMMMMMMM
MMMMMMMMMMM Author: Alex Budding                                     MMMMMMMMMMM
MMMMMMMMMMM E-mail: pwdr@wetterhorn.nl                               MMMMMMMMMMM
MMMMMMMMMMM This software has been released under the GPL License    MMMMMMMMMMM 
MMMMMMMMMMM                                                          MMMMMMMMMMM
MMMMMMMMMMMMMMMMMMMMMMMMMMMMMMMMMMMMMMMMMMMMMMMMMMMMMMMMMMMMMMMMMMMMMMMMMMMMMMMM
MMMMMMMMMMMMMMMMMMMMMMMMMMMMMMMMMMMMMMMMMMMMMMMMMMMMMMMMMMMMMMMMMMMMMMMMMMMMMM*/

/////////////////////////////////////////////////////////////////////////////////
//
// Always manually add the 'PwdrPrintData.ino' file by Sketch >> Add File...
// When the Arduino IDE asks to replace the file, cancel. Move the file to 
// a different location and add again from this location. When the file is   
// updated by the PwdrPrecosssor, it's now automatically updated.
//
/////////////////////////////////////////////////////////////////////////////////
// The void spray_ink is adapted from DIY Inkjet Printer Firmware written by 
// Nicholas C Lewis (2011), see thingiverse.com/thing:8542
/////////////////////////////////////////////////////////////////////////////////

// Inlcude libraries for stepper motor [http://www.open.com.au/mikem/arduino/AccelStepper]
// and the AVR library for using the flash memory of the microcontroller
#include <AccelStepper.h>
#include <avr/pgmspace.h>

// How many times a single spot is printed
const int saturation = 1;

// Bytes for the nozzle control
byte lower = B00000000;
byte upper = B0000;

// Define the size of the file that stores the print information,
// stored as follows: 
// width, height/#nozzles, number of elements per row (height/nozzles*width)
// This information is stored in the seperate file called printdata.ino
extern int printfilesize[];
extern prog_uchar printFileLower[][2000];
extern prog_uchar printFileUpper[][2000];

// Initilize stepper driver, 11 Direction and 12 Step
AccelStepper stepperX(1, 53, 52);  
AccelStepper stepperZ2(1, 47, 46);
AccelStepper stepperY(1, 49, 48);
AccelStepper stepperZ1(1, 51, 50);
// Watch out, this one is wired different!
AccelStepper stepperR(1, 44, 45);

// Stepper speed and accelaration
float stepperMaxSpeed = 22000.0;
float stepper_R_MaxSpeed = 22000.0;
float stepperMaxAccelaration = 1000000.0;

// Size of steps for stepper motors
const int stepX = 21;    // 0.09433962264 mm  per step (5*9.6mm*PI/1600)
const int stepY = 500;      // 0.09433962264 mm  per step (5*9.6mm*PI/1600)
const int stepZ = 95;      // 0.1mm per full stap (10*0.01)

// Size of steps when jogging
const int jogStepY = 1000;
const int jogStepX = 500;
const int jogStepZ = 250;

// Size of machine in steps. Type long because number of steps > int (2^15)
const long build_piston_width = 11000/stepX;    //2000/stepX;         // total width: 14800
const long build_piston_length = 28000/stepY;   // total length 76000
const long distance_roller_nozzle = 34000;      
const long piston_depth = printfilesize[2];     // The depth of the part is defined by the preprocessor
const long build_piston_end_stop = 76000;          // Absolute end of the machine

// Variable for positioning
long jogvar = 0;
long jogvar2 = 0;

void setup(){  

  // Initialize Onboard LED and extra button
  pinMode(5, INPUT); 
  pinMode(13, OUTPUT);
  
  // Initilize the ink pins (22 to 33) and stepper pins (44-53)
  for (int i=22; i<=53; i++) {
    pinMode(i, OUTPUT);
  } 
  
  // Reset the ports for the printer nozzles
  PORTA = B00000000;
  PORTC = B00000000;
 
  // Start serial communication, baud rate 9600
  Serial.begin(9600);

  // Initialise stepper motors
  stepperX.setMaxSpeed(stepperMaxSpeed);
  stepperX.setAcceleration(stepperMaxAccelaration);
  stepperY.setMaxSpeed(stepperMaxSpeed);
  stepperY.setAcceleration(stepperMaxAccelaration);
  stepperZ1.setMaxSpeed(stepperMaxSpeed);
  stepperZ1.setAcceleration(stepperMaxAccelaration);
  stepperZ2.setMaxSpeed(stepperMaxSpeed);
  stepperZ2.setAcceleration(stepperMaxAccelaration);
  stepperR.setMaxSpeed(stepperMaxSpeed);
  stepperR.setAcceleration(stepper_R_MaxSpeed);
  // Set the speeed for compactin the powder (- for right direction)
  stepperR.setSpeed(-stepper_R_MaxSpeed);   

  // Return the carriage to 0,-14000 position, first set the Y to -14000
  stepperY.setCurrentPosition(-distance_roller_nozzle);
  homeXY();

  Serial.println("Printer ready");
  Serial.println("-- SAFE TO CONNECT POWER --");
     
}

void loop(){

  if (Serial.available()){
    char serialbutton = Serial.read();

    if (serialbutton == 'p'){        

      // Switch on the LED
      analogWrite(13, 255);

      // Safety measure, return carriage to 0,0 position
      homeXY();

      Serial.println("Print started"); 

      for (long z=1;z<2*piston_depth;z++){

        for (long y=1; y<=printfilesize[1]; y++){    //build_piston_length; y++){

          for (long x=1; x<=printfilesize[0]; x++){  //build_piston_width
                    
              // Move steps in X direction, reverse direction from left to right
              // when the Y position is even.
              if(y % 2){
                stepperX.runToNewPosition(stepperX.currentPosition()-(stepX));//2));
              } 
              else {
                stepperX.runToNewPosition(stepperX.currentPosition()+(stepX));//2));
             }
              
             // If the button on the protoshield is pushed, the printing process is aborted.
             if (analogRead(54) == 0){
               // Reset the ports for the printer nozzles, prevent destroying the nozzles
               PORTA = B00000000;
               PORTC = B00000000;      
               Serial.println("Printing aborted");
               delay(1000);
               Serial.println("Please disconnect power and reset Arduino");
               // Hence breaking all the loops would demand for a couple of extra statements, it's
               // eassier and less resource demanding to put the Arduino controller in a infinite loop
               while(1) { }
               
              } else {
  
               for (int i=0; i<saturation; i++){   
               // Fire the nozzles, as many times as prescribed
               // Read the print files stored in the flash memory
                
                 if(y % 2){
                   lower  =  pgm_read_byte_near(&printFileLower[y-1][x-1]);
                   upper =  pgm_read_byte_near(&printFileUpper[y-1][x-1]);
                 } else {
                   lower  =  pgm_read_byte_near(&printFileLower[y-1][printfilesize[0]-(x-1)]);
                   upper =  pgm_read_byte_near(&printFileUpper[y-1][printfilesize[0]-(x-1)]); 
                  }               
                    spray_ink(lower,upper);
                }
              }
            }
          
          if (y % 2){
            stepperY.runToNewPosition(stepperY.currentPosition()-(stepY));//2));
          } else {
           stepperY.runToNewPosition(stepperY.currentPosition()-(stepY));//12));
          }
          
        }
        
        if(z % 2){
          homeXY();
        } else { 
          // Message to serial to indicate layer is done and the show overall progress
          Serial.print("Layer "); Serial.print(z); Serial.print(" of "); Serial.print(piston_depth)-1; Serial.println(" printed");
          
          // When the complete layer is printed, a new layer of powder is deposited
          make_new_powder_layer();
        }
      }   

    // Handle all other incoming communication
    
    // Backward x-axis
    } 
    else if(serialbutton == 'x'){
      jogX(-jogStepX);
      //          Serial.println("Jog -X done");
      Serial.println(stepperX.currentPosition());
      // Forward x-axis
    } 
    else if(serialbutton == 'X'){
      jogX(jogStepX);
      //          Serial.println("Jog X+ done");
      Serial.println(stepperX.currentPosition());
      // Backward y-axis
    } 
    else if(serialbutton == 'y'){
      jogY(-jogStepY);
      Serial.println(stepperY.currentPosition());
//      Serial.println("Jog -Y done");
      // Forward y-axis
    } 
    else if(serialbutton == 'Y'){
      jogY(jogStepY);
      Serial.println(stepperY.currentPosition());
//      Serial.println("Jog Y+ done");
      // Backward z-axis
    } 
    else if(serialbutton == 'z'){
      jogZ(-jogStepZ);
      Serial.println("Jog -Z done");
      // Forward z-axis
    } 
    else if(serialbutton == 'Z'){
      jogZ(jogStepY);
      Serial.println("Jog Z+ done");
      // Home the carriage
    }  
     else if(serialbutton == '1'){
      jogZ1(-jogStepZ);
      Serial.println("Jog Z1+ done");
    } 
    else if(serialbutton == 'q'){
      jogZ1(jogStepZ);
      Serial.println("Jog Z1- done");
    } 
    else if(serialbutton == '2'){
      jogZ2(-jogStepZ);
      Serial.println("Jog Z2+ done");
    } 
    else if(serialbutton == 'w'){
      jogZ2(jogStepZ);
      Serial.println("Jog Z2+ done");
    } 
    else if(serialbutton == 'h'){
      homeXY();
      // Reset the stepper counters
    } 
    else if(serialbutton == 'r'){
      resetStepperPositions();
      Serial.println("Stepper counters reset");
      // Make a new powder layer
    } 
    else if(serialbutton == 'n'){
      make_new_powder_layer();
      Serial.println("New powder layer deposited");
    } 
    else if(serialbutton == 's'){
      jogZ2(jogStepZ);
      jogY(-distance_roller_nozzle);
      jogX(-6000);
      resetStepperPositions();
      Serial.println("Nozzle at start position");
    } 
    else if(serialbutton == 'R'){
      stepperR.runToNewPosition(stepperR.currentPosition()+5000);
      Serial.println("Roller");
    }
    else if(serialbutton == 'E'){
      stepperY.runToNewPosition(-build_piston_end_stop+stepY);
      Serial.println("Carriage near end of piston");
    }  else {
      Serial.println("Unknown command"); 
    }
  }
  

  // Blink the LED to show the Arduino is idle
  digitalWrite(13,HIGH);
  delay(18);
  digitalWrite(13,LOW);
  delay(18);
}

void spray_ink( byte lower_nozzles, byte upper_nozzles) {
//lower_nozzles = 1-8  - PORTA
  for(int i = 0; i <= 7; i++){
    byte mask = 1<<i;
    if(lower_nozzles & mask){
      PORTA |= mask; delayMicroseconds(5);
      PORTA &= ~mask; delayMicroseconds(1);
    }
  } 
//upper_nozzles = 9-12 - PORTC using pins 4,5,6,7 so 4-7 not 0-3
  for(int i = 4; i <= 7; i++){
    byte mask = 1<<i;
    if(upper_nozzles<<3 & mask){
      PORTC |= mask; delayMicroseconds(5);
      PORTC &= ~mask; delayMicroseconds(1);
    }
  }
//wait to be sure we don't try to fire nozzles to fast and burn them out
  delayMicroseconds(450); 
}

void make_new_powder_layer(){
  // In case the X is not at zero
  stepperX.runToNewPosition(0);
  jogZ2(-jogStepZ);
  // Lower the powder bin to prevent powder from scooping
  jogZ1(2*jogStepZ);
  //Jog Y to the end of the powder bin
  stepperY.runToNewPosition(-build_piston_end_stop);
  // And move the powder bin back again
  jogZ1(-2*jogStepZ);
  // Move both pistons simultaniously
  jogZ(stepZ);
   // Spread the powder over the piston, roller rotate with constant spee   
  stepperY.moveTo(0);
  // Let the roller rotate untill 
  while (stepperY.currentPosition() != 0){
    stepperR.runSpeed();
    stepperY.run();
  }
  // Return carriage to (0,-14000)
  // Move piston down to prevent scewing
  jogZ2(jogStepZ);
  stepperY.runToNewPosition(-distance_roller_nozzle);
}

// Jog in X direction
void jogX(long jogDirStep){
  // Define direction, larger than 1 means clockwise
  if(jogDirStep>0){
    jogvar = stepperX.currentPosition()+abs(jogDirStep);
  } else {
    jogvar = stepperX.currentPosition()-abs(jogDirStep);
  }
  // Check wether it's allowed to take a step
  if ((jogvar >= 0) || (jogvar <= build_piston_width)){
    stepperX.runToNewPosition(jogvar); 
  } else { 
    Serial.println("jog X impossible");
  }
}

// Jog in Y direction
void jogY(long jogDirStep){
  if(jogDirStep>0){
    jogvar = stepperY.currentPosition()+abs(jogDirStep);
  } else {
    jogvar = stepperY.currentPosition()-abs(jogDirStep);
  }
  if ((jogvar >= 0) || (jogvar <= build_piston_length)){
    stepperY.runToNewPosition(jogvar); 
  } else { 
    Serial.println("jog Y impossible");
  }
}

// Jog of Z1 piston
void jogZ1(long jogDirStep){
  if(jogDirStep>0){
    jogvar = stepperZ1.currentPosition()+abs(jogDirStep);
  } else {
    jogvar = stepperZ1.currentPosition()-abs(jogDirStep);
  }
  if ((jogvar >= 0) || (jogvar <= piston_depth)){
    stepperZ1.runToNewPosition(jogvar); 
  } else { 
    Serial.println("jog Z1 impossible");
  }
}

// Jog of Z2 piston
void jogZ2(long jogDirStep){
  if(jogDirStep>0){
    jogvar = stepperZ2.currentPosition()+abs(jogDirStep);
  } else {
    jogvar = stepperZ2.currentPosition()-abs(jogDirStep);
  }
  if ((jogvar >= 0) || (jogvar <= piston_depth)){
    stepperZ2.runToNewPosition(jogvar); 
  } else { 
    Serial.println("jog Z2 impossible");
  }
}

// Combined jog in Z direction for both pistons
void jogZ(long jogDirStep){
  if(jogDirStep>0){
    jogvar = stepperZ1.currentPosition()-abs(1.5*jogDirStep);
    jogvar2 = stepperZ2.currentPosition()+abs(jogDirStep);
  } else {
    jogvar = stepperZ1.currentPosition()+abs(1.5*jogDirStep);
    jogvar2 = stepperZ2.currentPosition()-abs(jogDirStep);
  }
  if ((jogvar >= 0) || (jogvar <= piston_depth)){
    stepperZ1.moveTo(jogvar); 
    stepperZ2.moveTo(jogvar2); 
  } else { 
    Serial.println("jog Z2 impossible");
  }
  while (stepperZ1.currentPosition() != jogvar || stepperZ2.currentPosition() != jogvar2){
    stepperZ1.run();
    stepperZ2.run(); 
  }
}

// Reset the positions of the steppers. This acts as a margin
// for the printer, making it possible to fill the pistons with
// powder and stopping the 
void resetStepperPositions(){
  stepperX.setCurrentPosition(0);
  stepperY.setCurrentPosition(-distance_roller_nozzle);
  stepperZ1.setCurrentPosition(0);
  stepperZ2.setCurrentPosition(0);
  Serial.println("Stepper counters reset");  
}

void homeXY(){
  // Return the XY-carriage to 0,0  
  stepperX.moveTo(0); 
  stepperY.moveTo(-distance_roller_nozzle); 

  while (stepperY.currentPosition() != -distance_roller_nozzle || stepperX.currentPosition() != 0) {
    stepperX.run();
    stepperY.run();
  }
  Serial.println("Carriage homing");
}

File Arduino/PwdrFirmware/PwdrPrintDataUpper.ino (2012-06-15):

PROGMEM prog_uchar printFileUpper[][2000] ={{0, 0, 0, 0, 0, 0, 0, 0, 0, 0, 0, 0, 0, 0, 0, 0, 0, 0, 0, 0, 0, 0, 0, 0, 0, 0, 0, 0, 0, 0, 0, 0, 0, 0, 0, 0, 0, 0, 0, 0, 0, 0, 0, 0, 0, 0, 0, 0, 0, 0, 0, 0, 0, 0, 0, 0, 0, 0, 0, 0, 0, 0, 0, 0, 0, 0, 0, 0, 0, 0, 0, 0, 0, 0, 0, 0, 0, 0, 0, 0, 0, 0, 0, 0, 0, 0, 0, 0, 0, 0, 0, 0, 0, 0, 0, 0, 0, 0, 0, 0, 0, 0, 0, 0, 0, 0, 0, 0, 0, 0, 0, 0, 0, 0, 0, 0, 0, 0, 0, 0, 0, 0, 0, 0, 0, 0, 0, 0, 0, 0, 0, 0, 0, 0, 0, 0, 0, 0, 0, 0, 0, 0, 0, 0, 0, 0, 0, 0, 0, 0, 0, 0, 0, 0, 0, 0, 0, 0, 0, 0, 0, 0, 0, 0, 0, 0, 0, 0, 0, 0, 0, 0, 0, 0, 0, 0, 0, 0, 0, 0, 0, 0, 0, 0, 0, 0, 0, 0, 0, 0, 0, 0, 0, 0, 0, 0, 0, 0, 0, 0, 0, 0, 0, 0, 0, 0, 0, 0, 0, 0, 0, 0, 0, 0, 0, 0, 0, 0, 0, 0, 0, 0, 0, 0, 0, 0, 0, 0, 0, 0, 0, 0, 0, 0, 0, 0, 0, 0, 0, 0, 0, 0, 0, 0, 0, 0, 0, 0, 0, 0, 0, 0, 0, 0, 0, 0, 0, 0, 0, 0, 0, 0, 0, 0, 0, 0, 0, 0, 0, 0, 0, 0, 0, 0, 0, 0, 0, 0, 0, 0, 0, 0, 0, 0, 0, 0, 0, 0, 0, 0, 0, 0, 0, 0, 0, 0, 0, 0, 0, 0, 0, 0, 0, 0, 0, 0, 0, 0, 0, 0, 0, 0, 0, 0, 0, 0, 0, 0, 0, 0, 0, 0, 0, 0, 0, 0, 0, 0, 0, 0, 0, 0, 0, 0, 0, 0, 0, 0, 0, 0, 0, 0, 0, 0, 0, 0, 0, 0, 0, 0, 0, 0, 0, 0, 0, 0, 0, 0, 0, 0},{0, 0, 0, 0, 0, 0, 0, 0, 0, 0, 0, 0, 0, 0, 0, 0, 0, 0, 0, 0, 0, 0, 0, 0, 0, 0, 0, 0, 0, 0, 0, 0, 0, 0, 0, 0, 0, 0, 0, 0, 0, 0, 0, 0, 0, 0, 0, 0, 0, 0, 0, 0, 0, 0, 0, 0, 0, 0, 0, 0, 0, 0, 0, 0, 0, 0, 0, 0, 0, 0, 0, 0, 0, 0, 0, 0, 0, 0, 0, 0, 0, 0, 0, 0, 0, 0, 0, 0, 0, 0, 0, 0, 0, 0, 0, 0, 0, 0, 0, 0, 0, 0, 0, 0, 0, 0, 0, 0, 0, 0, 0, 0, 0, 0, 0, 0, 0, 0, 0, 0, 0, 0, 0, 0, 0, 0, 0, 0, 0, 0, 0, 0, 0, 0, 0, 0, 0, 0, 0, 0, 0, 0, 0, 0, 0, 0, 0, 0, 0, 0, 0, 0, 0, 0, 0, 0, 0, 0, 0, 0, 0, 0, 0, 0, 0, 0, 0, 0, 0, 0, 0, 0, 0, 0, 0, 0, 0, 0, 0, 0, 0, 0, 0, 0, 0, 0, 0, 0, 0, 0, 0, 0, 0, 0, 0, 0, 0, 0, 0, 0, 0, 0, 0, 0, 0, 0, 0, 0, 0, 0, 0, 0, 0, 0, 0, 0, 0, 0, 0, 0, 0, 0, 0, 0, 0, 0, 0, 0, 0, 0, 0, 0, 0, 0, 0, 0, 0, 0, 0, 0, 0, 0, 0, 0, 0, 0, 0, 0, 0, 0, 0, 0, 0, 0, 0, 0, 0, 0, 0, 0, 0, 0, 0, 0, 0, 0, 0, 0, 0, 0, 0, 0, 0, 0, 0, 0, 0, 0, 0, 0, 0, 0, 0, 0, 0, 0, 0, 0, 0, 0, 0, 0, 0, 0, 0, 0, 0, 0, 0, 0, 0, 0, 0, 0, 0, 0, 0, 0, 0, 0, 0, 0, 0, 0, 0, 0, 0, 0, 0, 0, 0, 0, 0, 0, 0, 0, 0, 0, 0, 0, 0, 0, 0, 0, 0, 0, 0, 0, 0, 0, 0, 0, 0, 0, 0, 0, 0, 0, 0, 0, 0, 0, 0, 0, 0, 0, 0, 0, 0, 0},{0, 0, 0, 0, 0, 0, 0, 0, 0, 0, 0, 0, 0, 0, 0, 0, 0, 0, 0, 0, 0, 0, 0, 0, 0, 0, 0, 0, 0, 0, 0, 0, 0, 0, 0, 0, 0, 0, 0, 0, 0, 0, 0, 0, 0, 0, 0, 0, 0, 0, 0, 0, 0, 0, 0, 0, 0, 0, 0, 0, 0, 0, 0, 0, 0, 0, 0, 0, 0, 0, 0, 0, 0, 0, 0, 0, 0, 0, 0, 0, 0, 0, 0, 0, 0, 0, 0, 0, 0, 0, 0, 0, 0, 0, 0, 0, 0, 0, 0, 0, 0, 0, 0, 0, 0, 0, 0, 0, 0, 0, 0, 0, 0, 0, 0, 0, 0, 0, 0, 0, 0, 0, 0, 0, 0, 0, 0, 0, 0, 0, 0, 0, 0, 0, 0, 0, 0, 0, 0, 0, 0, 0, 0, 0, 0, 0, 0, 0, 0, 0, 0, 0, 0, 0, 0, 0, 0, 0, 0, 0, 0, 0, 0, 0, 0, 0, 0, 0, 0, 0, 0, 0, 0, 0, 0, 0, 0, 0, 0, 0, 0, 0, 0, 0, 0, 0, 0, 0, 0, 0, 0, 0, 0, 0, 0, 0, 0, 0, 0, 0, 0, 0, 0, 0, 0, 0, 0, 0, 0, 0, 0, 0, 0, 0, 0, 0, 0, 0, 0, 0, 0, 0, 0, 0, 0, 0, 0, 0, 0, 0, 0, 0, 0, 0, 0, 0, 0, 0, 0, 0, 0, 0, 0, 0, 0, 0, 0, 0, 0, 0, 0, 0, 0, 0, 0, 0, 0, 0, 0, 0, 0, 0, 0, 0, 0, 0, 0, 0, 0, 0, 0, 0, 0, 0, 0, 0, 0, 0, 0, 0, 0, 0, 0, 0, 0, 0, 0, 0, 0, 0, 0, 0, 0, 0, 0, 0, 0, 0, 0, 0, 0, 0, 0, 0, 0, 0, 0, 0, 0, 0, 0, 0, 0, 0, 0, 0, 0, 0, 0, 0, 0, 0, 0, 0, 0, 0, 0, 0, 0, 0, 0, 0, 0, 0, 0, 0, 0, 0, 0, 0, 0, 0, 0, 0, 0, 0, 0, 0, 0, 0, 0, 0, 0, 0, 0, 0, 0, 0, 0, 0},{0, 0, 0, 0, 0, 0, 0, 0, 0, 0, 0, 0, 0, 0, 0, 0, 0, 0, 0, 0, 0, 0, 0, 0, 0, 0, 0, 0, 0, 0, 0, 0, 0, 0, 0, 0, 0, 0, 0, 0, 0, 0, 0, 0, 0, 0, 0, 0, 0, 0, 0, 0, 0, 0, 0, 0, 0, 0, 0, 0, 0, 0, 0, 0, 0, 0, 0, 0, 0, 0, 0, 0, 0, 0, 0, 0, 0, 0, 0, 0, 0, 0, 0, 0, 0, 0, 0, 0, 0, 0, 0, 0, 0, 0, 0, 0, 0, 0, 0, 0, 0, 0, 0, 0, 0, 0, 0, 0, 0, 0, 0, 0, 0, 0, 0, 0, 0, 0, 0, 0, 0, 0, 0, 0, 0, 0, 0, 0, 0, 0, 0, 0, 0, 0, 0, 0, 0, 0, 0, 0, 0, 0, 0, 0, 0, 0, 0, 0, 0, 0, 0, 0, 0, 0, 0, 0, 0, 0, 0, 0, 0, 0, 0, 0, 1, 1, 1, 1, 1, 1, 1, 1, 1, 1, 1, 1, 1, 1, 1, 1, 1, 1, 1, 1, 1, 1, 1, 1, 1, 1, 1, 0, 0, 0, 0, 0, 0, 0, 0, 0, 0, 0, 0, 0, 0, 0, 0, 0, 0, 0, 0, 0, 0, 0, 0, 0, 0, 0, 0, 0, 0, 0, 0, 0, 0, 0, 0, 0, 0, 0, 0, 0, 0, 0, 0, 0, 0, 0, 0, 0, 0, 0, 0, 0, 0, 0, 0, 0, 0, 0, 0, 0, 0, 0, 0, 0, 0, 0, 0, 0, 0, 0, 0, 0, 0, 0, 0, 0, 0, 0, 0, 0, 0, 0, 0, 0, 0, 0, 0, 0, 0, 0, 0, 0, 0, 0, 0, 0, 0, 0, 0, 0, 0, 0, 0, 0, 0, 0, 0, 0, 0, 0, 0, 0, 0, 0, 0, 0, 0, 0, 0, 0, 0, 0, 0, 0, 0, 0, 0, 0, 0, 0, 0, 0, 0, 0, 0, 0, 0, 0, 0, 0, 0, 0, 0, 0, 0, 0, 0, 0, 0, 0, 0, 0, 0, 0, 0, 0, 0, 0, 0, 0, 0, 0, 0, 0, 0, 0, 0, 0},{0, 0, 0, 0, 0, 0, 0, 0, 0, 0, 0, 0, 0, 0, 0, 0, 0, 0, 0, 0, 0, 0, 0, 0, 0, 0, 0, 0, 0, 0, 0, 0, 0, 0, 0, 0, 0, 0, 0, 0, 0, 0, 0, 0, 0, 0, 0, 0, 0, 0, 0, 0, 0, 0, 0, 0, 0, 0, 0, 0, 0, 0, 0, 0, 0, 0, 0, 0, 0, 0, 0, 0, 0, 0, 0, 0, 0, 0, 0, 0, 0, 0, 0, 0, 0, 0, 0, 0, 0, 0, 0, 0, 0, 0, 0, 0, 0, 0, 0, 0, 0, 0, 0, 0, 0, 0, 0, 0, 0, 0, 0, 0, 0, 0, 0, 0, 0, 0, 0, 0, 0, 1, 1, 3, 3, 7, 7, 15, 15, 15, 15, 15, 15, 15, 15, 15, 15, 15, 15, 15, 15, 15, 15, 15, 15, 15, 15, 15, 15, 15, 15, 15, 15, 15, 15, 15, 15, 15, 15, 15, 15, 15, 15, 15, 15, 15, 15, 15, 15, 15, 15, 15, 15, 15, 15, 15, 15, 15, 15, 15, 15, 15, 15, 15, 15, 15, 15, 15, 15, 15, 15, 15, 15, 15, 15, 15, 15, 15, 15, 15, 15, 15, 15, 15, 15, 15, 15, 15, 15, 15, 15, 15, 15, 15, 15, 15, 15, 15, 15, 15, 15, 15, 15, 15, 15, 15, 15, 15, 7, 7, 3, 3, 1, 1, 0, 0, 0, 0, 0, 0, 0, 0, 0, 0, 0, 0, 0, 0, 0, 0, 0, 0, 0, 0, 0, 0, 0, 0, 0, 0, 0, 0, 0, 0, 0, 0, 0, 0, 0, 0, 0, 0, 0, 0, 0, 0, 0, 0, 0, 0, 0, 0, 0, 0, 0, 0, 0, 0, 0, 0, 0, 0, 0, 0, 0, 0, 0, 0, 0, 0, 0, 0, 0, 0, 0, 0, 0, 0, 0, 0, 0, 0, 0, 0, 0, 0, 0, 0, 0, 0, 0, 0, 0, 0, 0, 0, 0, 0, 0, 0, 0, 0, 0, 0, 0, 0, 0, 0, 0, 0, 0, 0, 0, 0, 0, 0, 0, 0, 0, 0, 0, 0, 0, 0, 0, 0, 0, 0, 0, 0},{0, 0, 0, 0, 0, 0, 0, 0, 0, 0, 0, 0, 0, 0, 0, 0, 0, 0, 0, 0, 0, 0, 0, 0, 0, 0, 0, 0, 0, 0, 0, 0, 0, 0, 0, 0, 0, 0, 0, 0, 0, 0, 0, 0, 0, 0, 0, 0, 0, 0, 0, 0, 0, 0, 0, 0, 0, 0, 0, 0, 0, 0, 0, 0, 0, 0, 0, 0, 0, 0, 0, 0, 0, 0, 0, 0, 0, 0, 0, 0, 0, 0, 0, 0, 0, 0, 0, 0, 0, 0, 0, 0, 0, 0, 0, 0, 0, 0, 0, 0, 1, 3, 3, 7, 15, 15, 15, 15, 15, 15, 15, 15, 15, 15, 15, 15, 15, 15, 15, 15, 15, 15, 15, 15, 15, 15, 15, 15, 15, 15, 15, 15, 15, 15, 15, 15, 15, 15, 15, 15, 15, 15, 15, 15, 15, 15, 15, 15, 15, 15, 15, 15, 15, 15, 15, 15, 15, 15, 15, 15, 15, 15, 15, 15, 15, 15, 15, 15, 15, 15, 15, 15, 15, 15, 15, 15, 15, 15, 15, 15, 15, 15, 15, 15, 15, 15, 15, 15, 15, 15, 15, 15, 15, 15, 15, 15, 15, 15, 15, 15, 15, 15, 15, 15, 15, 15, 15, 15, 15, 15, 15, 15, 15, 15, 15, 15, 15, 15, 15, 15, 15, 15, 15, 15, 15, 15, 15, 15, 15, 15, 15, 15, 15, 15, 15, 15, 15, 15, 15, 15, 15, 15, 15, 15, 15, 15, 15, 15, 15, 15, 15, 7, 3, 3, 1, 0, 0, 0, 0, 0, 0, 0, 0, 0, 0, 0, 0, 0, 0, 0, 0, 0, 0, 0, 0, 0, 0, 0, 0, 0, 0, 0, 0, 0, 0, 0, 0, 0, 0, 0, 0, 0, 0, 0, 0, 0, 0, 0, 0, 0, 0, 0, 0, 0, 0, 0, 0, 0, 0, 0, 0, 0, 0, 0, 0, 0, 0, 0, 0, 0, 0, 0, 0, 0, 0, 0, 0, 0, 0, 0, 0, 0, 0, 0, 0, 0, 0, 0, 0, 0, 0, 0, 0, 0, 0, 0, 0, 0, 0, 0, 0, 0, 0, 0, 0, 0, 0, 0, 0, 0},{0, 0, 0, 0, 0, 0, 0, 0, 0, 0, 0, 0, 0, 0, 0, 0, 0, 0, 0, 0, 0, 0, 0, 0, 0, 0, 0, 0, 0, 0, 0, 0, 0, 0, 0, 0, 0, 0, 0, 0, 0, 0, 0, 0, 0, 0, 0, 0, 0, 0, 0, 0, 0, 0, 0, 0, 0, 0, 0, 0, 0, 0, 0, 0, 0, 0, 0, 0, 0, 0, 0, 0,
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

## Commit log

2012-05-11 Initial commit. Added all SolidWorks, Arduino and Processing files for the Model 0.1 Pwdr machine
    [A6A51M018DF0606.SLDPRT, A7Z44MPSD04MAF.SLDPRT, Arduino Mega 2560.SLDPRT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]
2012-05-24 Removed bugs in the homeXY function and moved file height declaration to the external files
    [PwdrFirmware.ino, PwdrPrintData.ino, PwdrPrintDataUpper.ino]
2012-06-15 Big cleanup for files. Added dxf files for laser cutting. Edited the readme
    [A6A51M018DF0606.SLDPRT, A7Z44MPSD04MAF.SLDPRT, Arduino Mega 2560.SLDPRT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]
2012-07-03 Updated print file
    Everything is now super much faster! Wow!
2012-07-03 Revert "Updated print file"
    This reverts commit 404ce8c807aa018abc06a91c077a8f86c690153a.
    [PwdrPrintData.ino]
2012-08-10 Added electronics schemes
    [Pwdr Protoshield + Stepper Drivers.fzz]
2012-08-15 Added the lasercut drawing of the 5mm acrylic plate
2012-09-05 New Processing software, including STL conversion. The Arduino software hasn't been updated yet
2012-09-05 Updated the correct V0.3 code, Arduino not updated yet
    [Pwdr_GUI_V0_3.pde, Pwdr_GUI_V0_3.pde.pde, SimpleSlice.pde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]
2012-09-12 Bug fixes in serial communication and moved data files
    [Pwdr_GUI_V0_3.pde, SimpleSlice.pde, convertModel.pde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]
2012-09-17 Inserted missing jigsaw and encreased hole sizes for cables
2012-09-18 Bug fixes in the laser cut drawings
2012-09-24 Added Eagle schematic layout for the electronics
    [Pwdr-Circuit-0.2.sch]
2012-09-24 New binary print files, eassier to read with the Arduino
2012-09-25 New firmware for Arduino. Reading print file from SD card. Check pins! Not tested!
2012-09-25 Bug fix in binary file storage
    [Pwdr_GUI_V0_3.pde, convertModel.pde, voidsController.ino]
2012-09-25 Bug fix and removed Mac App
    [Pwdr_GUI_V0_3.pde, convertModel.pde, voidsController.ino]
2012-09-26 Bug fix in settings
    [mouseClicked.pde]
2012-10-10 Arduino and Processing ready for SD card. Changed file names and added config file
2012-10-12 Updated the 5mm laser cut drawing
2012-10-16 Removed bugs from converter and improved printing by added adaptable saturation, the first 4 layers have 1.5 time the saturation
    [PwdrFirmware2_0.ino, Pwdr_GUI_V0_3.pde, SimpleSlice.pde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]
2012-10-17 bug fixes for 3D printing
    [Pwdr_GUI_V0_3.pde, SimpleSlice.pde, printFile.ino]
2012-10-18 Changed parameter for printing ZP131
2012-10-24 Bug fixes and improved UI
    [Pwdr_GUI_V0_3.pde, mouseClicked.pde]
2012-10-24 Added shutdown to schematic.
    [Pwdr-Circuit-0.2.sch]
2012-10-29 Save and read preferences from file
    [config.txt]
2012-11-12 Updated pull up pin
2013-01-17 Bug fix in the 5mm Acrylic plate
    [PwdrFirmware.ino, convertModel.pde]
2013-01-18 Hole size bronze bearing
2013-01-27 Updated Eagle files for schemes
    [Pwdr-Circuit-0.1.sch, Pwdr-Circuit-0.2.sch]
2013-02-19 Updated printer head connections
2013-02-19 Updated printer head connections (pdf)
2013-05-13 Increased size of print_data to avoid bug in STL conversion
    [convertModel.pde]
2013-08-26 Fixed an old bug under Windows causing to not load any STL file
    Ignore the deleted DAT files
2013-08-26 Savebyte() causes bug under Windows, method is changed.
    Need some cleaning up later to save quite some bytes
    [convertModel.pde]
2014-06-16 Bug in SolidWorks file, missing hole, SVG was OK.
    [Pwdr - Model 0.1 - Chassis2VAR.SLDPRT]
2015-06-27 Removed bug from electronic diagrams
    [Pwdr Protoshield + Stepper Drivers.fzz, Pwdr-Circuit-0.1.sch]
2015-06-27 Updated config
    [config.txt]
2015-06-27 Corrected wiring to HP Conn.
    [Pwdr-Circuit-0.1.sch]
